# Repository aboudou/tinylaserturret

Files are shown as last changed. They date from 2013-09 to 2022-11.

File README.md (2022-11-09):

TinyLaserTurret
===============

TinyLaserTurret is a simple ATtiny85 based laser turret, with Nunchuck control.

* [TinyLaserTurret in action](http://www.youtube.com/watch?v=AJifI_-Nt7g)

Requirements
------------

TinyLaserTurret use few items:

* An [ATtiny85](http://www.atmel.com/devices/attiny85.aspx) microcontroller.
* A [5V laser module](http://dx.com/p/genuine-new-wish-5mw-red-laser-module-5v-2-pack-10091).
* A [BCU-81](http://www.alliedelec.com/search/productdetail.aspx?SKU=R1017089) transistor to drive the laser module.
* A 330Ω resistor to drive BCU-81 transistor.
* A [pan & tilt mount with servos](http://dx.com/p/2-9g-servos-bracket-sensor-mount-pan-tilt-kit-for-gyro-translucent-blue-214081) to orient laser module.
* A [L78S05CV](http://www.alliedelec.com/search/productdetail.aspx?SKU=70013915) voltage regulator.
* Two 100 µF capacitors to filter voltage spike.
* Two 4.7kΩ pull-up resistors for I<sup>2</sup>C lines.
* A [WiiChuck](http://www.dfrobot.com/index.php?route=product/product&product_id=91) adapter.
* A [power](http://www.adafruit.com/products/368) adapter.
* And a 170 points breadboard, batteries, wires and a Wii Nunchuck.

The full bill of materials is available in the file “docs/bom.xlsx”

Optionnaly, you'll need a 3D printer to build the turret.

You can find all the schematics and PCB into “doc/TinyLaserTurret.fzz”, to open with [Fritzing](http://fritzing.org/).

How to use TinyLaserTurret
--------------------------

TinyLaserTurret needs an ATtiny85 controller running at 8MHz. Once you have build the assembly, you have to connect to it:

* Batteries to the power adapter (from 7V to 12V).
* Wii Nunchuck to the WiiChuck adapter.

Then you will be able to control the turret with Nunchuck's analog joystick, and fire the laser with Nunchuck's Z button. And your cat will be happy :)

Wiring diagram
--------------

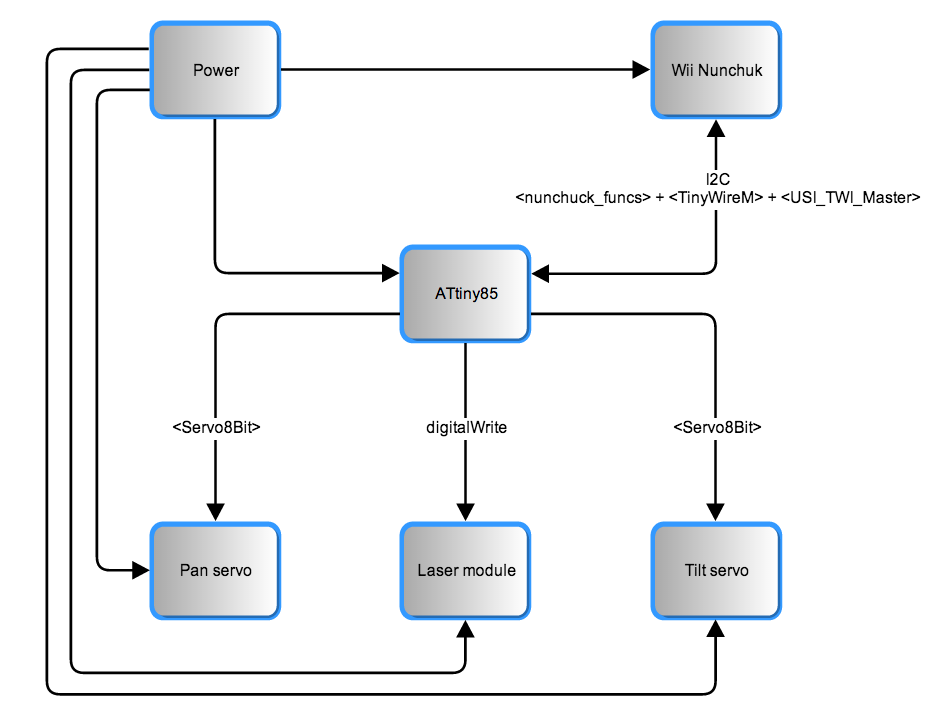
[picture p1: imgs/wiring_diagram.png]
Diagram


The breadboard assembly and schematics
--------------------------------------

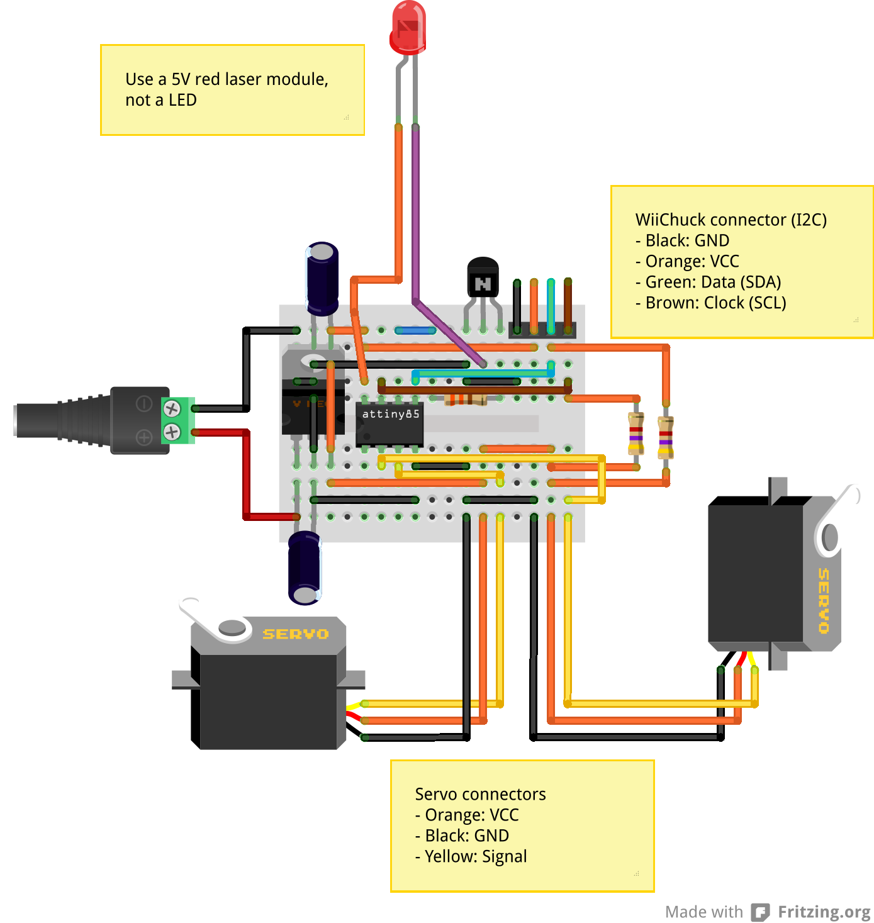
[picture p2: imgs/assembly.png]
Breadboard assembly

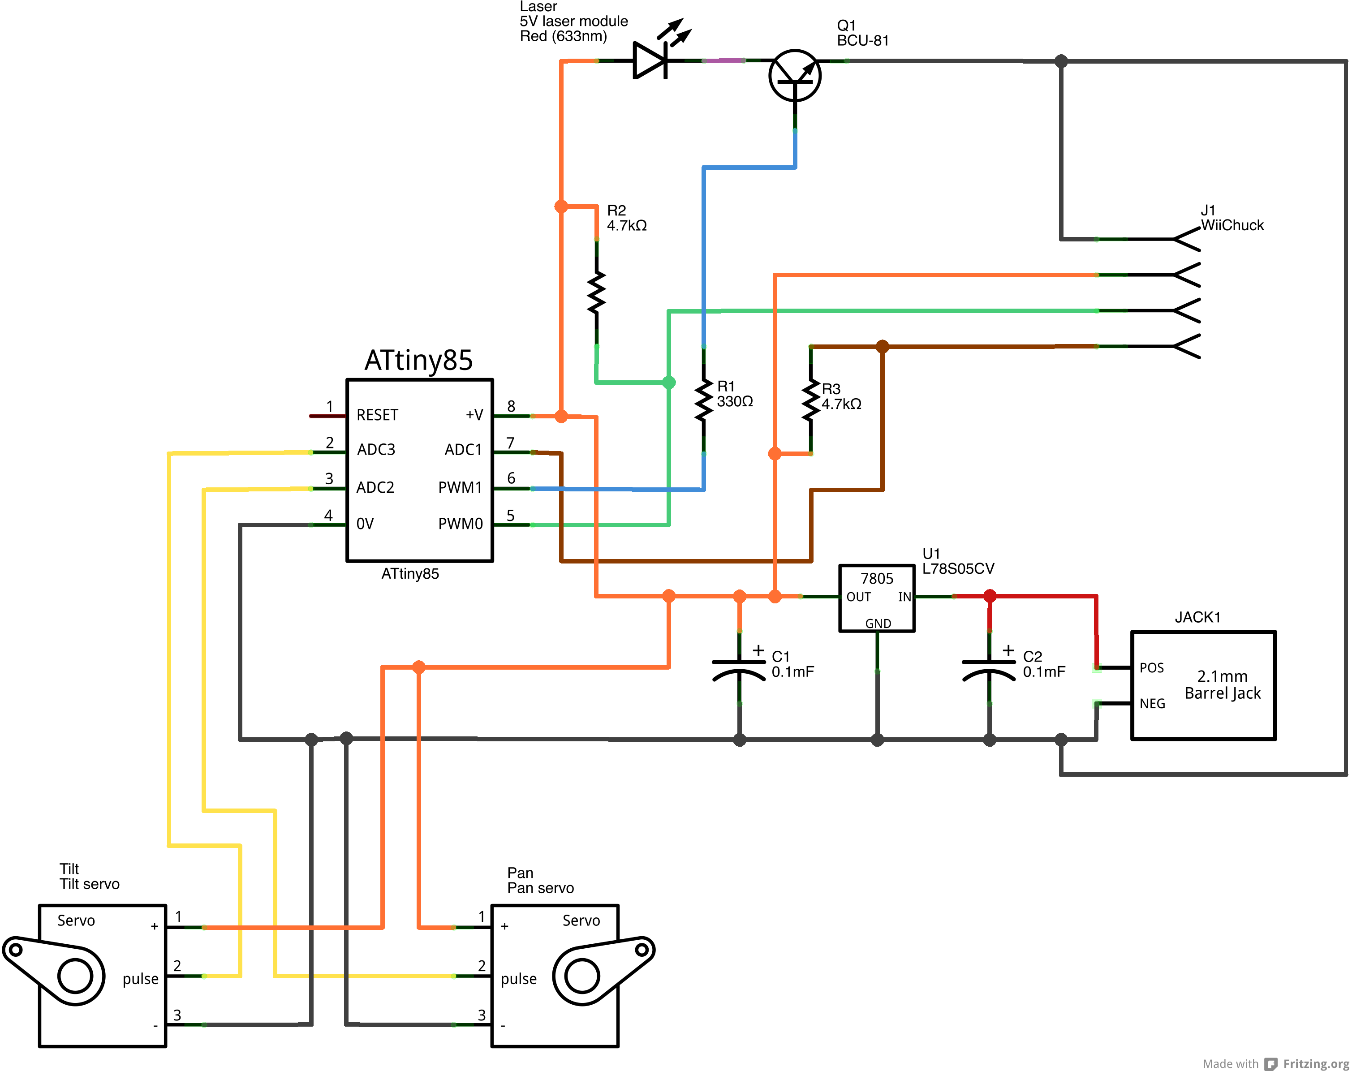
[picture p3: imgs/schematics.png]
Schematics


Building the turret
-------------------

I provide 3D parts to build the turret. These 3D parts were sized for the specified bill of materials. If you use different items, you'll have to adapt the 3D parts. You'll find inside “3d_parts” folder the following files:

* 3d_assembly.skp: 3D file to show how to build the turret.
* 3d_assembly.stl: same as above, for automatic preview from GitHub site.
* laser_support.skp: 3D file of the laser module support.
* laser_support.stl: same as above, to be uploaded to 3D printer.
* leg.skp: 3D file for turret legs.
* leg.stl: same as above, to be uploaded to 3D printer. You'll have to print four of those.
* main_support.skp: 3D file of the main support, where pan & tilt servos and breadboard will be put.
* main_support.stl: same as above, to be uploaded to 3D printer.

“.skp” files were made with [Trimble Sketchup Make 2013](http://www.sketchup.com/download/all)

3D parts are not made for the PCB assembly. I plan to make a specific version later.

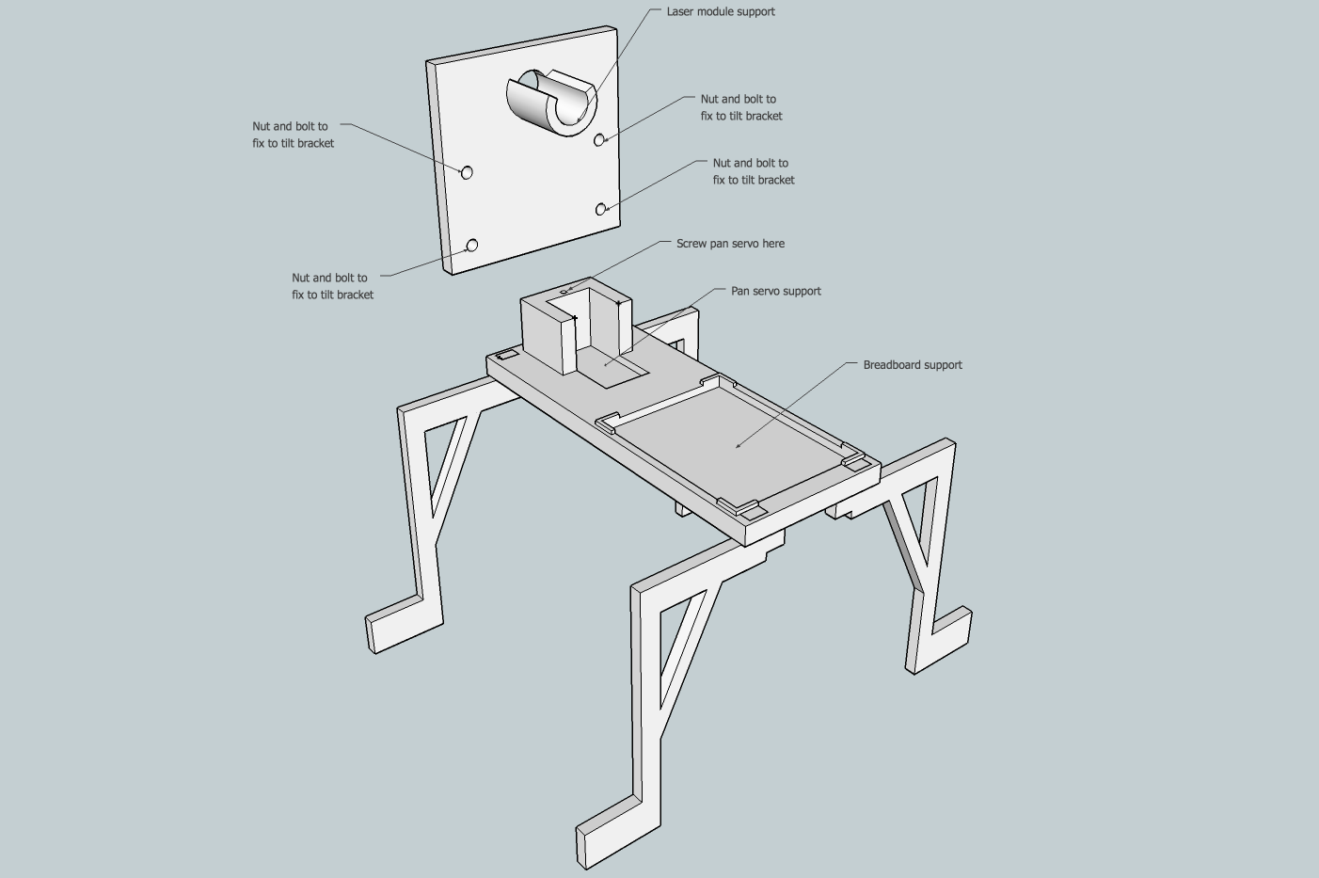
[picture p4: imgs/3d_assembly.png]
3D assembly


Notes
-----
TinyLaserTurret uses third party libraries, which are included with the project:

* [Servo8Bit](http://www.cunningturtle.com/attiny4585-servo-library/): A library which allows ATtiny microcontroller to drive servos.
* [TinyWireM](http://playground.arduino.cc/Code/USIi2c): An I<sup>2</sup>C library for ATtiny85. 
* [USI_TWI_Master](http://playground.arduino.cc/Code/USIi2c): Universal Serial Interface library for ATtiny85, used by TinyWireM. This library was modified to work with an 8MHz ATtiny85, and support I<sup>2</sup>C fast mode (400kHz) and standard mode (< 100kHz)
* [nunchuck_funcs](http://todbot.com/blog/2008/02/18/wiichuck-wii-nunchuck-adapter-available/): A library to communicate with Wii Nunchuck. It was modified to work with TinyWireM.

The live assembly
-----------------

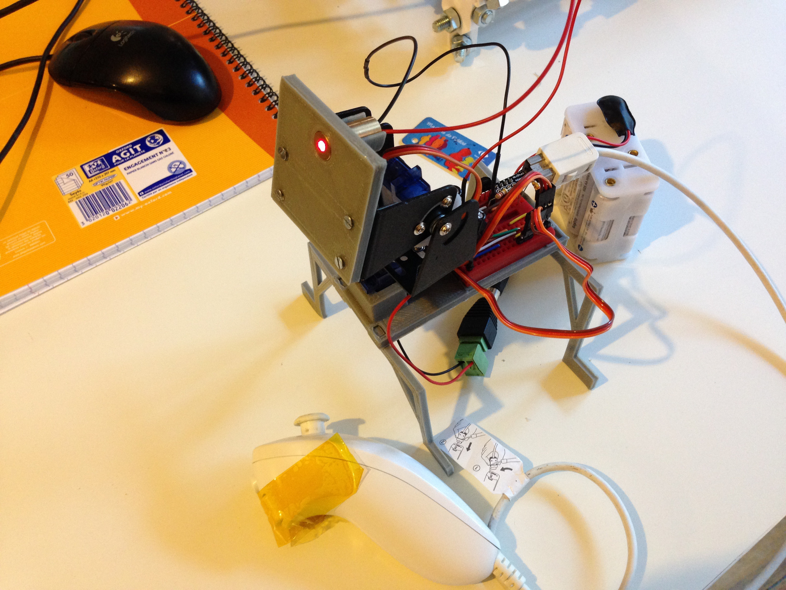
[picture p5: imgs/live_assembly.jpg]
Live assembly


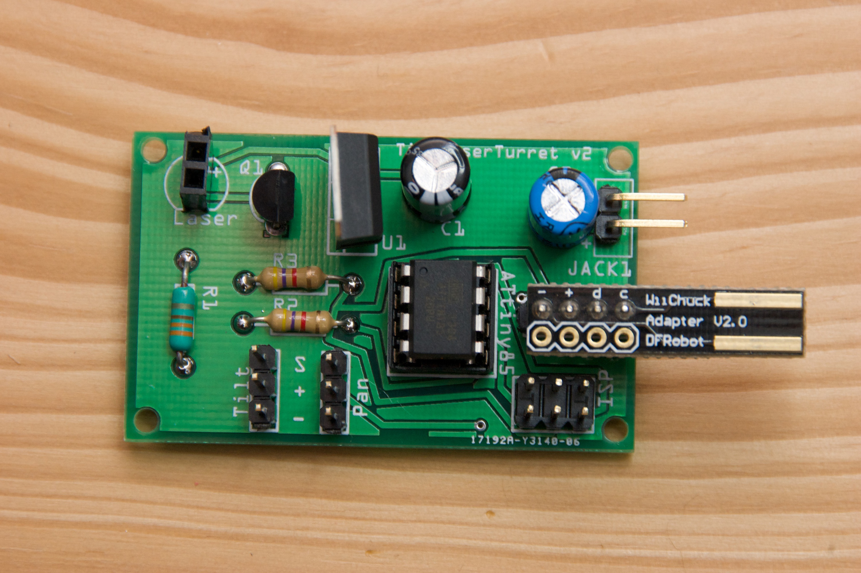
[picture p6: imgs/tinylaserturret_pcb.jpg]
PCB assembly


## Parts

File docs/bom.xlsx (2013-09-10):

Part | Quantity | URL
Breadboard (170 points) | 1 | http://dx.com/p/mini-prototype-printed-circuit-board-breadboard-green-140105
ATtiny85 | 1 | https://www.sparkfun.com/products/9378
BCU-81 | 1 | http://www.alliedelec.com/search/productdetail.aspx?SKU=R1017089
L78S05CV | 1 | http://www.alliedelec.com/search/productdetail.aspx?SKU=70013915
100 µF capacitor | 2 | http://www.alliedelec.com/search/productdetail.aspx?SKU=70186474
330Ω resistor | 1 | http://www.alliedelec.com/search/productdetail.aspx?SKU=70183332
4.7kΩ resistor | 2 | http://www.alliedelec.com/search/productdetail.aspx?SKU=70183356
Power adapter | 1 | http://www.adafruit.com/products/368
Pan & Tilt mount with servos | 1 | http://dx.com/p/2-9g-servos-bracket-sensor-mount-pan-tilt-kit-for-gyro-translucent-blue-214081
WiiChuck | 1 | http://www.dfrobot.com/index.php?route=product/product&product_id=91
Laser module | 1 | http://dx.com/p/genuine-new-wish-5mw-red-laser-module-5v-2-pack-10091
Additionnal
Wii Nunchuck
Batteries (from 7V to 12V)
Wires

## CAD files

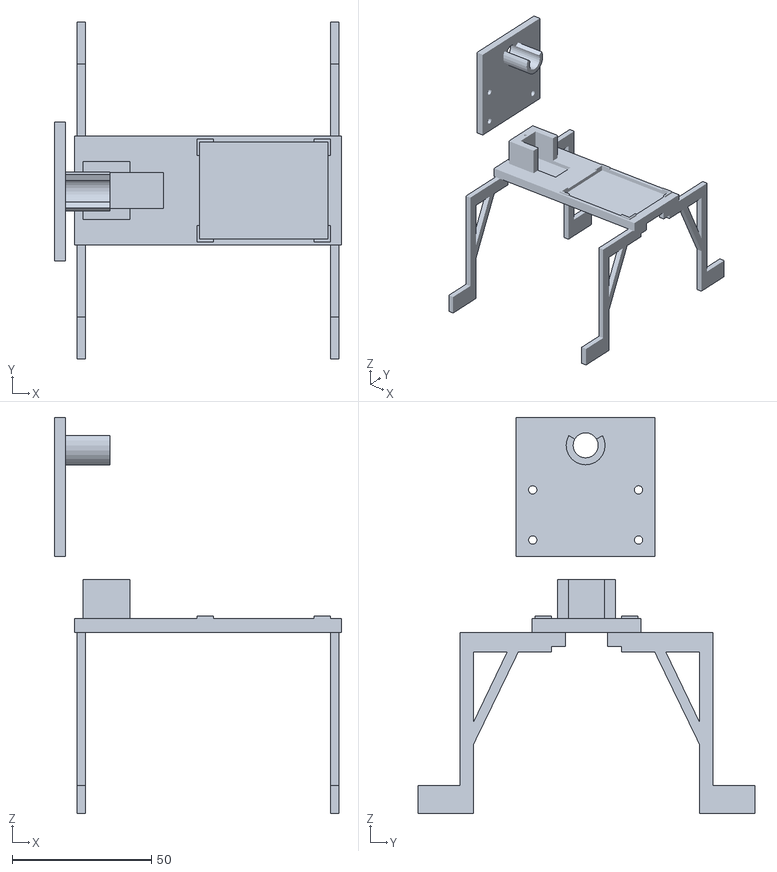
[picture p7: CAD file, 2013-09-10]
3d_parts/3d_assembly.stl
103.2 x 121.0 x 142.2

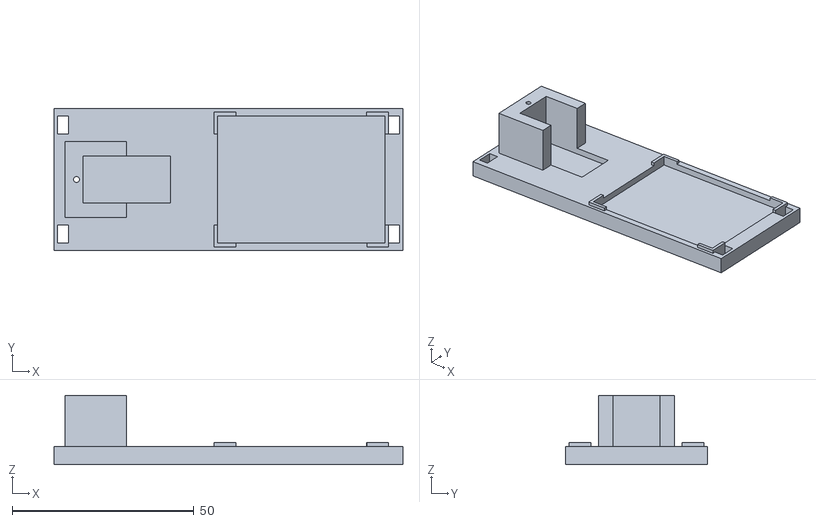
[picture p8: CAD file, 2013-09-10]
3d_parts/main_support.stl
96.0 x 39.0 x 19.0

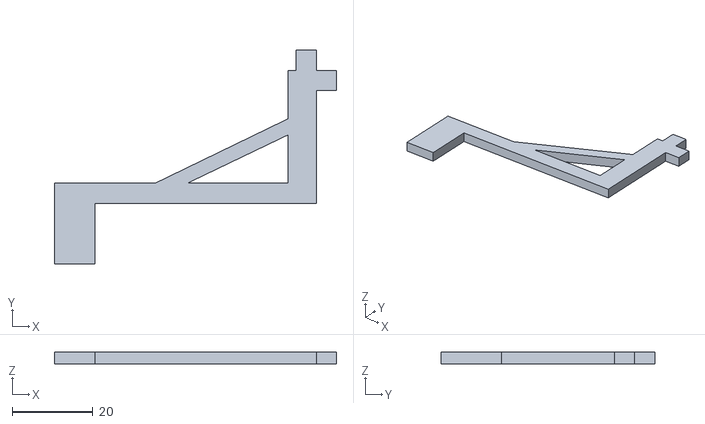
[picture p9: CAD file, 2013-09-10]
3d_parts/leg.stl
70.0 x 53.0 x 3.00

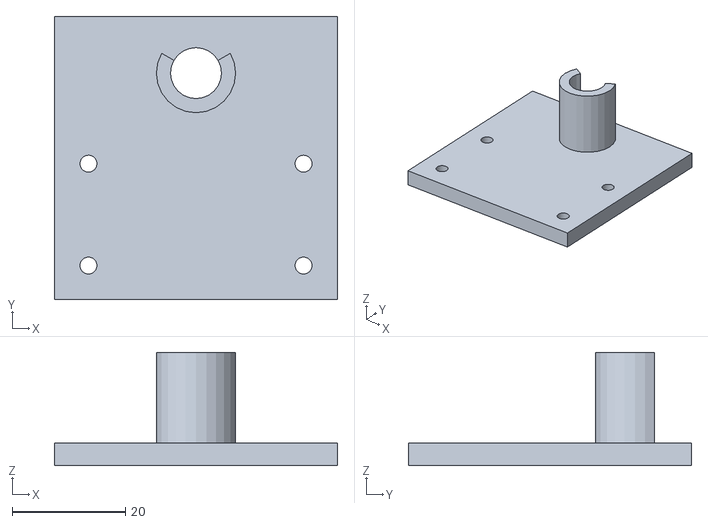
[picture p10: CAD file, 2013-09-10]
3d_parts/laser_support.stl
50.0 x 50.0 x 20.0

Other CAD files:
3d_parts/3d_assembly.skp
3d_parts/laser_support.skp
3d_parts/leg.skp
3d_parts/main_support.skp

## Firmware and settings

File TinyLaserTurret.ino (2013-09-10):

#include "TinyWireM.h"        // I2C library for ATtiny AVR
#include "nunchuck_funcs.h"   // Wii Nunchuck helper functions
#include "Servo8Bit.h"        // Servo library for ATtiny AVR

// Useful pins definitions
#define PANSERVOPIN 4         // Pan servo signal pin
#define TILTSERVOPIN 3        // Tilt servo signal pin
#define LASERPIN 1            // Laser module signal pin

// X axis values for nunchuck's joystick. You may adapt these for your own nunchuck
#define JOYXLEFT   34         // X Axis - Full left value
#define JOYXCENTER 133        // X Axis - Center value
#define JOYXRIGHT  230        // X Axis - Full right value

// Y axis values for nunchuck's joystick. You may adapt these for your own nunchuck
#define JOYYDOWN   36         // Y Axis - Full down value
#define JOYYCENTER 128        // Y Axis - Center value
#define JOYYUP     220        // Y Axis - Full up value

// Pan servo angle values. Adapt to fit your needs.
// You may need to swap left and right values depending on servo position.
#define PANSERVOLEFT    125   // Pan servo - Full left angle
#define PANSERVOCENTER  90    // Pan servo - Center angle
#define PANSERVORIGHT   55    // Pan servo - Full right angle

// Tilt servo angle values. Adapt to fit your needs.
// You may need to swap down and up values depending on servo position.
#define TILTSERVODOWN    55   // Tilt servo - Full down angle
#define TILTSERVOCENTER  90   // Tilt servo - Center angle
#define TILTSERVOUP      125  // Tilt servo - Full up angle


// Nunchuck useful variables
byte joyx, joyy, zbut;

// Servo declaration
Servo8Bit panServo;
Servo8Bit tiltServo;

void setup() {
  // Servo init
  panServo.attach(PANSERVOPIN);
  tiltServo.attach(TILTSERVOPIN);
  
  // Center servo
  panServo.write(PANSERVOCENTER);
  tiltServo.write(TILTSERVOCENTER);
  
  // Nunchuck init
  nunchuck_init();
  
  // Laser pin init
  pinMode(LASERPIN, OUTPUT);
  digitalWrite(LASERPIN, LOW);
  
}

void loop() {
  // Get nunchuck data
  nunchuck_get_data();
  
  joyx = nunchuck_joyx();
  joyy = nunchuck_joyy();
  zbut = nunchuck_zbutton();
  
  // Switch laser ON or OFF
  if (zbut == 1) {
    digitalWrite(LASERPIN, HIGH);
  } else {
    digitalWrite(LASERPIN, LOW);
  }
  
  
  // Move pan servo
  if (joyx == JOYXCENTER) {
    panServo.write(PANSERVOCENTER);
  } else if (joyx < JOYXCENTER) {
    byte position = map(joyx, JOYXLEFT, JOYXCENTER, PANSERVOLEFT, PANSERVOCENTER);
    panServo.write(position);
  } else {
    byte position = map(joyx, JOYXCENTER, JOYXRIGHT, PANSERVOCENTER, PANSERVORIGHT);
    panServo.write(position);
  }

  // Move tilt servo
  if (joyy == JOYYCENTER) {
    tiltServo.write(TILTSERVOCENTER);
  } else if (joyy < JOYYCENTER) {
    byte position = map(joyy, JOYYDOWN, JOYYCENTER, TILTSERVOUP, TILTSERVOCENTER);
    tiltServo.write(position);
  } else {
    byte position = map(joyy, JOYYCENTER, JOYYUP, TILTSERVOCENTER, TILTSERVODOWN);
    tiltServo.write(position);
  }
  
  delay(10);
}

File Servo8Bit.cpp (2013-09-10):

/*
 Servo8Bit.cpp - Interrupt driven Servo library for the Attiny45 and Attiny85 that uses an 8 bit timer.
 Version 0.7
 Copyright (c) 2011 Ilya Brutman.  All right reserved.

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
 You should have received a copy of the GNU Lesser General Public
 License along with this library; if not, write to the Free Software
 Foundation, Inc., 51 Franklin St, Fifth Floor, Boston, MA  02110-1301  USA
 */


/*

  A servo is activated by creating an instance of the Servo8Bit class passing the desired pin to the attach() method.
  The servos are pulsed in the background using the value most recently written using the write() method


  The methods are:

   Servo8Bit - Class for manipulating servo motors connected to Attiny pins.

   attach(pin)           - Attaches a servo motor to an i/o pin.
   attach(pin, min, max) - Attaches to a pin setting min and max values in microseconds
                           default min is 544, max is 2400

   write()               - Sets the servo angle in degrees.  (invalid angle that is valid as pulse in microseconds is treated as microseconds)
   writeMicroseconds()   - Sets the servo pulse width in microseconds
   read()                - Gets the last written servo pulse width as an angle between 0 and 180.
   readMicroseconds()    - Gets the last written servo pulse width in microseconds.
   attached()            - Returns true if there is a servo attached.
   detach()              - Stops an attached servos from pulsing its i/o pin.
 */


//TODO: Add an explaination of how this driver works. Include plenty of ASCII diagrams.

#include "Servo8Bit.h"
#include <inttypes.h>
#include <avr/io.h>
#include <avr/interrupt.h>
#include <Arduino.h>

//There two things defined in this file
// *The Servo Sequencer - which is the actual driver that generates pulses
// *The Servo class - which provides the Arduino-like interface



#ifdef USE_TIMER0
    #define TCNTn   TCNT0
    #define OCRnx   OCR0A
    #define OCFnx   OCF0A
    #define OCIEnx  OCIE0A
#endif

#ifdef USE_TIMER1
    #define TCNTn   TCNT1
    #define OCRnx   OCR1A
    #define OCFnx   OCF1A
    #define OCIEnx  OCIE1A
#endif

// Trim Duration is about the total combined time spent inside the Compare Match ISR
// This time is in timer ticks, where each tick is always 8 microseconds.
#define TRIM_DURATION 4


//This is the driver class responsible for generating the servo control pulses
// This class is purely static.
class ServoSequencer
{
public:
    //=============================================================================
    // Servo Sequencer public functions
    //=============================================================================
    static uint8_t  registerServo();
    //              Reserves a slot for a servo in the pulse sequence

    static void     deregisterServo(uint8_t servoSlotNumber);
    //              Frees an occupied slot

    static void     setServoPulseLength(uint8_t servoNumber, uint16_t newLengthInMicroseconds);
    //              Updates the pulse length of a servo to a new value

    static uint16_t getServoPulseLength(uint8_t servoNumber);
    //              returns the pulse length of a servo in microseconds

    static void     setServoPin(uint8_t servoNumber, uint8_t newPin);
    //              Updates the pin that will be pulsed

    static void     enableDisableServo(uint8_t servoNumber, bool servoShouldBeEnabled);
    //              Enable or disable a servo in a slot. A pulse is not generated for a servo slot that is disabled.

    static bool     isEnabled(uint8_t servoNumber);
    //              returns true is the servo is enabled

    inline static void timerCompareMatchISR();
    //              Handles a timer compare match.
    //              Should only be called when the timer compare match interrupt fires.

    //=============================================================================
    // Servo Sequencer public constants
    //=============================================================================
    static const uint8_t kInvalidServoIndex = 0xFF;



private:
    //=============================================================================
    // Servo Sequencer types
    //=============================================================================
    //This enum defines the states of the Servo Sequencer
    enum SequencerState_t
    {
        WAITING_FOR_512_MARK,
        WAITING_TO_SET_PIN_LOW,
        WAITING_FOR_2048_MARK,
        WAITING_TO_SET_PIN_HIGH
    };

    //This struct defines a single servo slot
    struct ServoEntry
    {
        uint8_t  pulseLengthInTicks;    //length of pulse in ticks after offset is applied
        uint8_t  pin;                   //which pin to pulse on portB
        bool     enabled;               //True when this servo should be pulsed
        bool     slotOccupied;          //True when this servo entry is allocated to a servo
    };

    //=============================================================================
    // Servo Sequencer private variables
    //=============================================================================
    static const    uint16_t          kMaxNumberOfServosSupported = 5;  //The number of servos to support. See NOTE1 below.
    static volatile SequencerState_t  state;                            //The current state of the driver
    static          bool              timerIsSetup;                     //True if the timer used by this driver was configured
    static          bool              servoArrayIsInited;               //True if the servo Registry array was initialized with default values.
    static          ServoEntry        servoRegistry[kMaxNumberOfServosSupported]; //The array of servo slots
    static volatile uint8_t           servoIndex;                       //The index of the current servo slot we are working with.
                                                                        //With 5 servos, we go through the whole servoRegistry every 20 milliseconds exactly.

    //=============================================================================
    // Servo Sequencer private functions
    //=============================================================================
    //This is a purely static class. Disallow making instances of this class.
    ServoSequencer();              //private constructor
    static void servoTimerSetup(); //Configures the timer used by this driver
    static void setupTimerPrescaler(); //helper function to setup the prescaler
    static void initServoArray();  //sets default values to each element of the servoRegistry array

};//end ServoSequencer
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

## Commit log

2013-09-10 Initial import
    [3d_assembly.skp, 3d_assembly.stl, TinyLaserTurret.fzz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]
2014-11-15 PCB assembly
    [TinyLaserTurret.fzz]
